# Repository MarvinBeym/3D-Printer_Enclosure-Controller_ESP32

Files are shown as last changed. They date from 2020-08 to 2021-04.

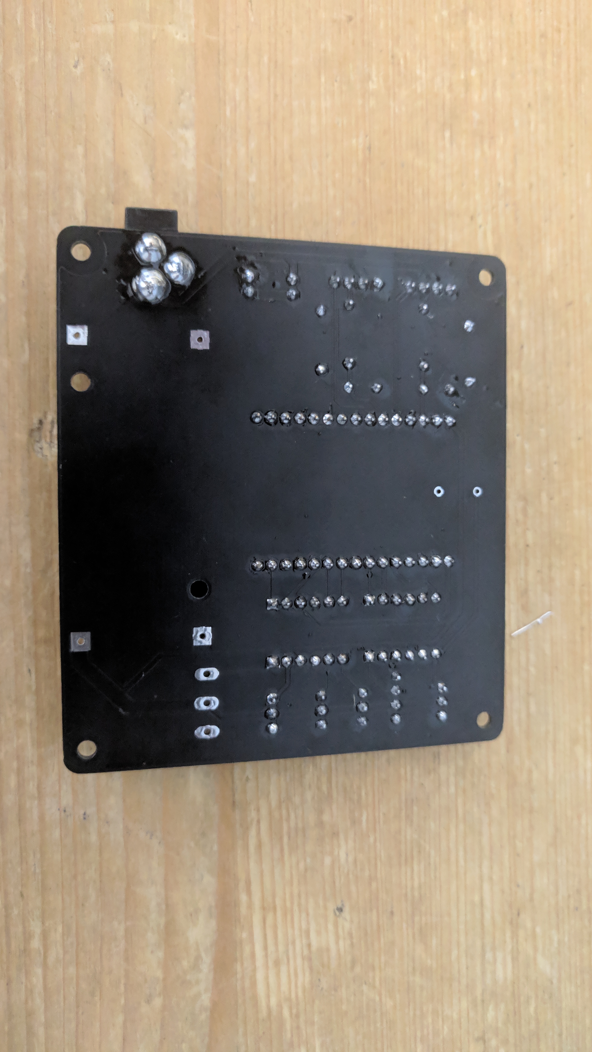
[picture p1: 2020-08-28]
Images/PCB_Fully-Assembled_Back.jpg

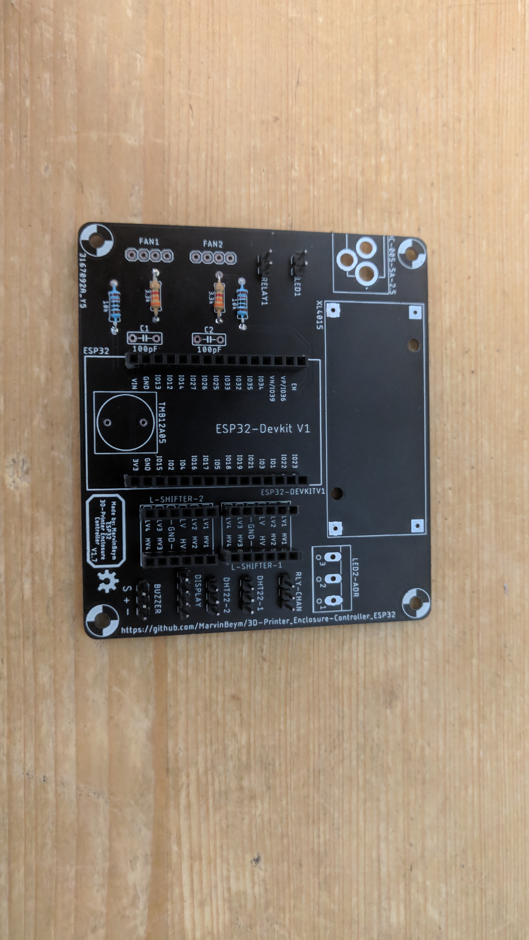
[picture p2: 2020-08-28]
Images/PCB_Assembling.jpg

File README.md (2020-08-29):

# 3D Printer Enclosure Controller ESP32


***
This is an enclosure controller for 3d printers that runs on the dual core ESP32.

- It uses a Nextion NX4832T035 3.5inch 480px320p color touch TFT display.
- It also includes a simple Webinterface made with ESPUI for quick access without having to go to the display.

- ***For detailed information and images please see the [Wiki](https://github.com/MarvinBeym/3D-Printer_Enclosure-Controller_ESP32/wiki "Wiki").***
- ***STL files for 3D-Printing can be found on [Thingiverse](https://www.thingiverse.com/thing:4582196 "Thingiverse")***
***
You can currently choose between 2 versions.
1. The older cnc version
This is a bit older (the first one I made). Features haven't changed yet.
This is the version you want If you want to mill the pcb with a cnc mill because it is single side and has wider traces to make it easier for your mill.
2. The newest, pretiest pcb version
This is supposed to be made by a pcb factory like jlcpcb
It has text on it for all the components.
It also looks way better (I recommend ordering in black :D)

If you choose 2. -> I ordered mine from JLCPCB. The Gerber files are inside the Eagle folder (Gerber(vx.x.x).7z)
These were exported with the premade jlcpcb double sided cam processor. So you can just upload them to jlcpcb and order them.

***This project consists of 4 parts.***
1. The ESP32 software.
2. The Nextion display software (text, icons, images, ...).
3. The PCB.
4. The 3D Printed case to house everything.

***Features of this controller are:***
- 2x temperature and humidity sensors (DHT22).
- 2x 4-pin pwm fans.
- 1x Buzzer for alarms, warnings and such (currently not implemented as of v1.3.1).
- 1x 12v led strip connection controlled by a relay. This is usefull if you want to have a single color (like white).
- 1x 5V WS2812B single addressable led strip

***Software features:***
- ESPUI webinterface
- WifiManager creates a hotspot you can connect to that will make it possible to set the wifi network to connect to on boot.
- All values that can be changed can also be stored to flash. These values will be retrieved at boot and only saved using button pressed to prevent flash wear.
- Displaying of fan speed and percent.
- The possibility to change the speed of fans from 0% - 100%
- Displaying of sensor humidity and temperature
- Switching of 12v led strip.
- Graph for temperatures (only nextion display currently)
- Multiple modes choosable for WS2812B
  - (rainbow, fate, pulse, temperature (led strip is split in half showing temperature in color), running)
- Multiple colors choosable for WS2812B
- LCD Brighness
- LCD Sleep
- Temperature Warning and Danger 
  - (Currently do the same)
  - At some point Danger warning is supposed to do everything to make your notice something going wrong.
  - Like buzzer alarm, led blinking, display blinking and such. This is supposed to be used when something is seriously wrong > xyzTemperature.

***Notices:***
- The board uses a XL4015 buck converter which is rated for ~5A of power. 
- Make sure to choose an led strip that won't overload the converter. As this could lead to overheating.
- Also make sure to leave a bit of room for all other components like fans, 12v led strip, sensors and display.

- It is expecially important to make sure the Nextion display gets enough power.
- If your display starts showing weird graphics. DISCONNECT power immediately.
- Don't run the pcb from 5V pc usb port.
- Low current can destroy the display (although it never happened to me).

- Fan rpm could be off a bit as tacho reading is influenced by noise.
- The tacho ports both have an rc filter and most fans will work without a problem and will display the correct value.
- I have one fan (NF-F12 industrialPPC-3000) that will always display > 4500rpm. 
  - (should only have 3000rpm). 
  - I'm not sure if that is something caused by the fan itself.

***Credits:***
- Icons shown on the Nextion display are from https://icons8.com/

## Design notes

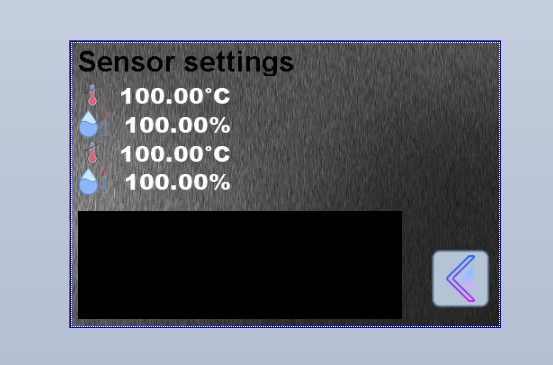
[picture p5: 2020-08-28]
Images/Software_Sensor-Page.jpg

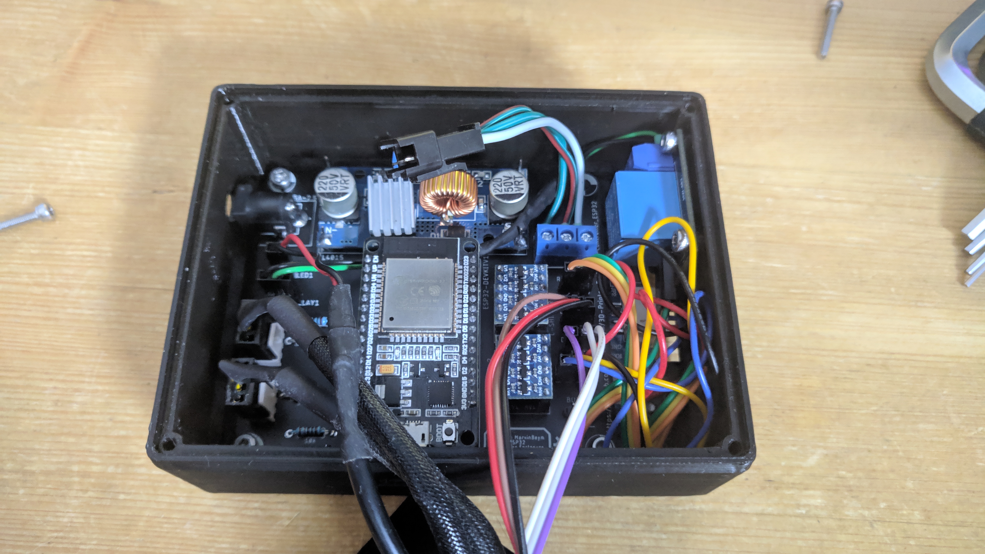
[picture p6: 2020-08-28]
Images/Enclosure_Inside_PCB.jpg

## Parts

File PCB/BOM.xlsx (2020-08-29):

This file includes all components needed to assemble the pcb
Based on pcb version: 1.7.1
PCB itself
Position | Amount | Name | Value | Where to get (mostly banggood -> depending on your location you should look at mouser, digikey or amazon)
R1, R3 |  | Resistor 0207/10 or probably any other | 3.3k Ohm | https://www.banggood.com/Wholesale-Geekcreit-600pcs-30-Kinds-Value-1-pencent-1-or-4W-Metal-Film-Resistor-Assorted-Kit-20pcs-Each-Value-p-53320.html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
R2, R4 |  | Resistor 0207/10 or probably any other | 10k Ohm
C1, C2 |  | Condensator C050-025X075 or probably any other | 100pF | https://www.banggood.com/1000Pcs-50-Value-50V-Ceramic-Capacitor-Assorted-Assortment-Kit-p-1032362.html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
XL4015 | 1 | XL4015 buck converter (not the single chip) |  | https://www.banggood.com/XL4015-5A-DC-DC-Step-Down-Adjustable-Power-Supply-Module-Buck-Converter-p-945599.html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
DC-005-5A-2.5 | 1 | DC-005-5A-2.5 dc jack | 5A | https://lcsc.com/product-detail/AC-DC-Power-Plugs-Receptacles_XKB-Connectivity-DC-005-5A-2-5_C381115.html
LED2-ADR | 1 | 3-Pin W237-103 = Screw terminal |  | https://www.banggood.com/10pcs-5mm-KF-301-3-Pin-PCB-Mount-Block-Screw-Terminal-NF-Connector-p-1136709.html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
IN+, IN-, OUT+, OUT- | 4 | 1-Pin Male Header |  | https://www.banggood.com/10Pcs-40-Pin-2_54mm-Male-Female-SIL-Socket-Row-Strip-PCB-Connector-p-953436.html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
LED1, RELAY1 | 2 | 2-Pin Male Header
RLY-CHAN, DHT22-1, DHT22-2, BUZZER | 4 | 3-Pin Male Header
DISPLAY, FAN1, FAN2 | 3 | 4-Pin Male Header
L-SHIFTER-1, L-SHIFTER-2 | 4 | 6-Pin Female Header
ESP32 | 2 | 15-Pin Female Header
Other components (You can choose less/none for some)
can be less | 2 | DHT22 Temperature and Humidity Sensor (with Pullup on sensor) (you can solder your own pullup | NEEDS PULLUP | https://www.banggood.com/3Pcs-AM2302-DHT22-Temperature-And-Humidity-Sensor-Module-p-1006452.html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
can be none | 1 | KY-019 (or any other) Relay (for 12V led |  | https://www.banggood.com/3Pcs-5V-Relay-5-12V-TTL-Signal-1-Channel-Module-High-Level-Expansion-Board-p-1178211.html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
can be less/none | 2 | 4-Pin PWM fans |  | Choose your own
needed | 1 | ESP32 (30pin) |  | https://www.banggood.com/Geekcreit-ESP32-WiFi+bluetooth-Development-Board-Ultra-Low-Power-Consumption-Dual-Cores-Pins-Unsoldered-p-1214159.html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
can be none | 1 | Buzzer (no use currently) either connected to BUZZER or below esp32 |  | Choose your own
needed | 1 | 12 Power supply >5A | Recommend > 5A | Choose your own
can be none | 1 | WS2812B | DONT BUY RGBW | Choose your own based on liking
can be none | 1 | 12v Led strip |  | Choose your own based on liking
needed | 2 | Bi-Direktional 4 Channel Level Shifter |  | https://www.banggood.com/Logic-Level-Converter-Bi-Directional-IIC-4-Way-Level-Conversion-Module-p-938774.html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

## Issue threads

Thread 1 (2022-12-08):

Nextion Display setup for NX4832F035 model

Pilgrim182551, 2022-12-08:
Mea Culpa ... I bought  NX4832F035 model instead of NX4832T035. Is there any chance to compile tft file for my "F" model? After applaying sd card with NextionDesignerFile.v1.3.1.tft display returns "Model does not match Device Model: NX4832F035_011R" ... Thx

MarvinBeym, 2022-12-29:
(Again note that this project is basically abandoned as Klipper makes everything easier & better)

1. Download the project => https://github.com/MarvinBeym/3D-Printer_Enclosure-Controller_ESP32 => "Code" => "Download Zip"
3. Extract somewhere (For this issue you only need the `Display` folder)
4. Download the NextionEditor: https://nextion.tech/nextion-editor/
5. Inside NextionEditor. Open the `NextionDesignerFile.HMI` file from the `Display` folder.
6. Once opened. At the top right you will find a `Device` button.
7. Switch to the `Device` menu
8. Change to the display you have.
9. You may have to change other things if the display is for example larger (most likely not relevant in this case)
10. Click on the `File` button at the top left of the main editor window.
11. Click on `TFT output`.
12. This should then give you the file to flash using the sd card

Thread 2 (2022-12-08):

Esp32 controller setup

Pilgrim182551, 2022-12-08:
VSC/Platformio compiler/linker return a number errors related to inconsistent libraries(littleFS) and process end up with red alert collect2.exe: error: ld returned 1 exit status
*** [.pio\build\esp32doit-devkit-v1\firmware.elf] Error 1

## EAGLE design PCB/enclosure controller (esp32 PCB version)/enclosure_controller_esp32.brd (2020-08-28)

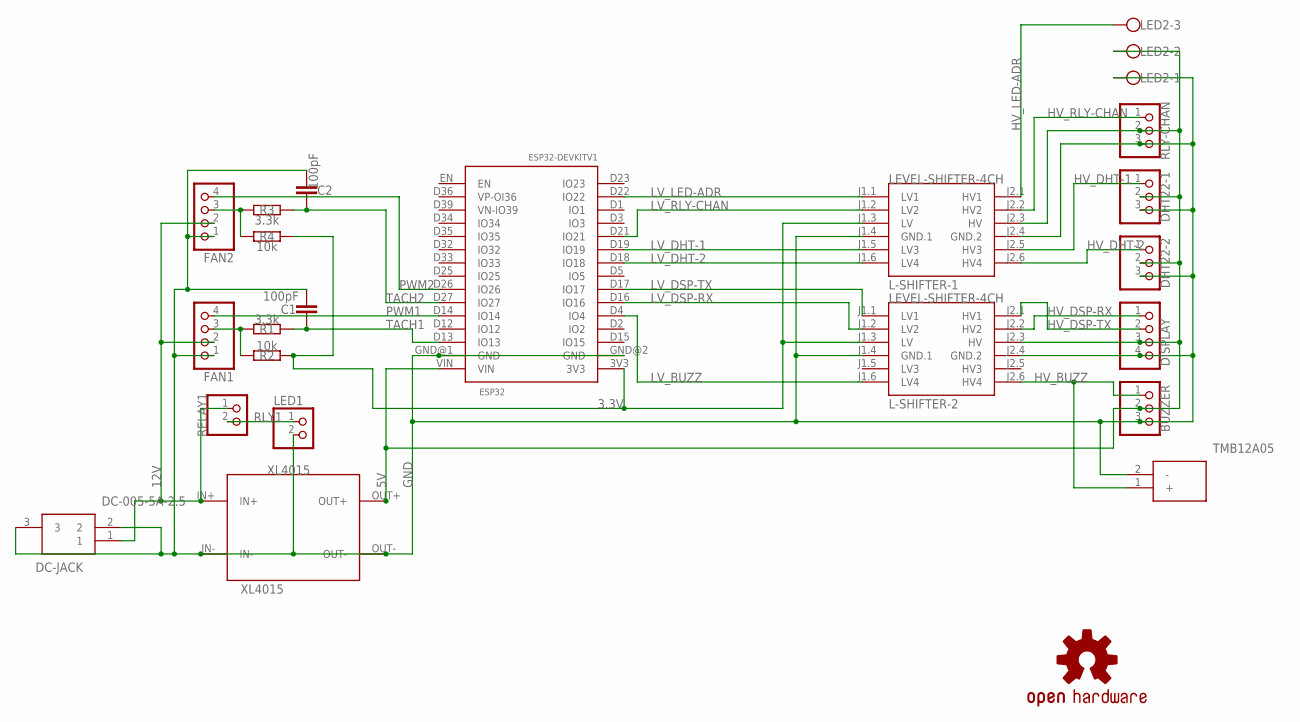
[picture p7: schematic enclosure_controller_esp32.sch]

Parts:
BUZZER: PINHD-1X3/OCT; 1X03/OCT
C1, C2: 100pF; C050-025X075
DC-JACK: DC-005-5A-2.5; DC0055A25
DHT22-1, DHT22-2: PINHD-1X3/OCT; 1X03/OCT
DISPLAY: PINHD-1X4/OCT; 1X04/OCT
ESP32: ESP32DEVKITV1; ESP32-DEVKITV1
FAN1, FAN2: PINHD-1X4/OCT; 1X04/OCT
L-SHIFTER-1, L-SHIFTER-2: LEVEL-SHIFTER-4CH
LED1: PINHD-1X2/OCT; 1X02/OCT
LED2: LED2-ADR; W237-103
LOGO1: OSHW-LOGOM; OSHW-LOGO-M
LS1: TMB12A05
R1, R3: 3.3k; 0207/10
R2, R4: 10k; 0207/10
RELAY1: PINHD-1X2/OCT; 1X02/OCT
RLY-CHAN: PINHD-1X3/OCT; 1X03/OCT
XL4015: XL4015

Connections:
3.3V: ESP32.3V3, L-SHIFTER-1.J1.3 (LV), L-SHIFTER-2.J1.3 (LV), R2.1, R4.1
5V: BUZZER.2, DHT22-1.2, DHT22-2.2, DISPLAY.3, ESP32.VIN, L-SHIFTER-1.J2.3 (HV), L-SHIFTER-2.J2.3 (HV), LED2.2, RLY-CHAN.2, XL4015.OUT+
12V: DC-JACK.1, FAN1.2, FAN2.2, RELAY1.1, XL4015.IN+
GND: BUZZER.3, C1.2, C2.1, DC-JACK.2, DC-JACK.3, DHT22-1.3, DHT22-2.3, DISPLAY.4, ESP32.GND@1 (GND), ESP32.GND@2 (GND), FAN1.1, FAN2.1, L-SHIFTER-1.J1.4 (GND.1), L-SHIFTER-1.J2.4 (GND.2), L-SHIFTER-2.J1.4 (GND.1), L-SHIFTER-2.J2.4 (GND.2), LED1.2, LED2.1, LS1.2 (-), RLY-CHAN.3, XL4015.IN-, XL4015.OUT-
HV_BUZZ: BUZZER.1, L-SHIFTER-2.J2.6 (HV4), LS1.1 (+)
HV_DHT-1: DHT22-1.1, L-SHIFTER-1.J2.5 (HV3)
HV_DHT-2: DHT22-2.1, L-SHIFTER-1.J2.6 (HV4)
HV_DSP-RX: DISPLAY.1, L-SHIFTER-2.J2.2 (HV2)
HV_DSP-TX: DISPLAY.2, L-SHIFTER-2.J2.1 (HV1)
HV_LED-ADR: L-SHIFTER-1.J2.1 (HV1), LED2.3
HV_RLY-CHAN: L-SHIFTER-1.J2.2 (HV2), RLY-CHAN.1
LV_BUZZ: ESP32.D4 (IO4), L-SHIFTER-2.J1.6 (LV4)
LV_DHT-1: ESP32.D19 (IO19), L-SHIFTER-1.J1.5 (LV3)
LV_DHT-2: ESP32.D18 (IO18), L-SHIFTER-1.J1.6 (LV4)
LV_DSP-RX: ESP32.D16 (IO16), L-SHIFTER-2.J1.2 (LV2)
LV_DSP-TX: ESP32.D17 (IO17), L-SHIFTER-2.J1.1 (LV1)
LV_LED-ADR: ESP32.D22 (IO22), L-SHIFTER-1.J1.1 (LV1)
LV_RLY-CHAN: ESP32.D21 (IO21), L-SHIFTER-1.J1.2 (LV2)
PWM1: ESP32.D14 (IO14), FAN1.4
PWM2: ESP32.D26 (IO26), FAN2.4
RLY1: LED1.1, RELAY1.2
TACH1: C1.1, ESP32.D13 (IO13), FAN1.3, R1.1, R1.2, R2.2
TACH2: C2.2, ESP32.D27 (IO27), FAN2.3, R3.1, R3.2, R4.2

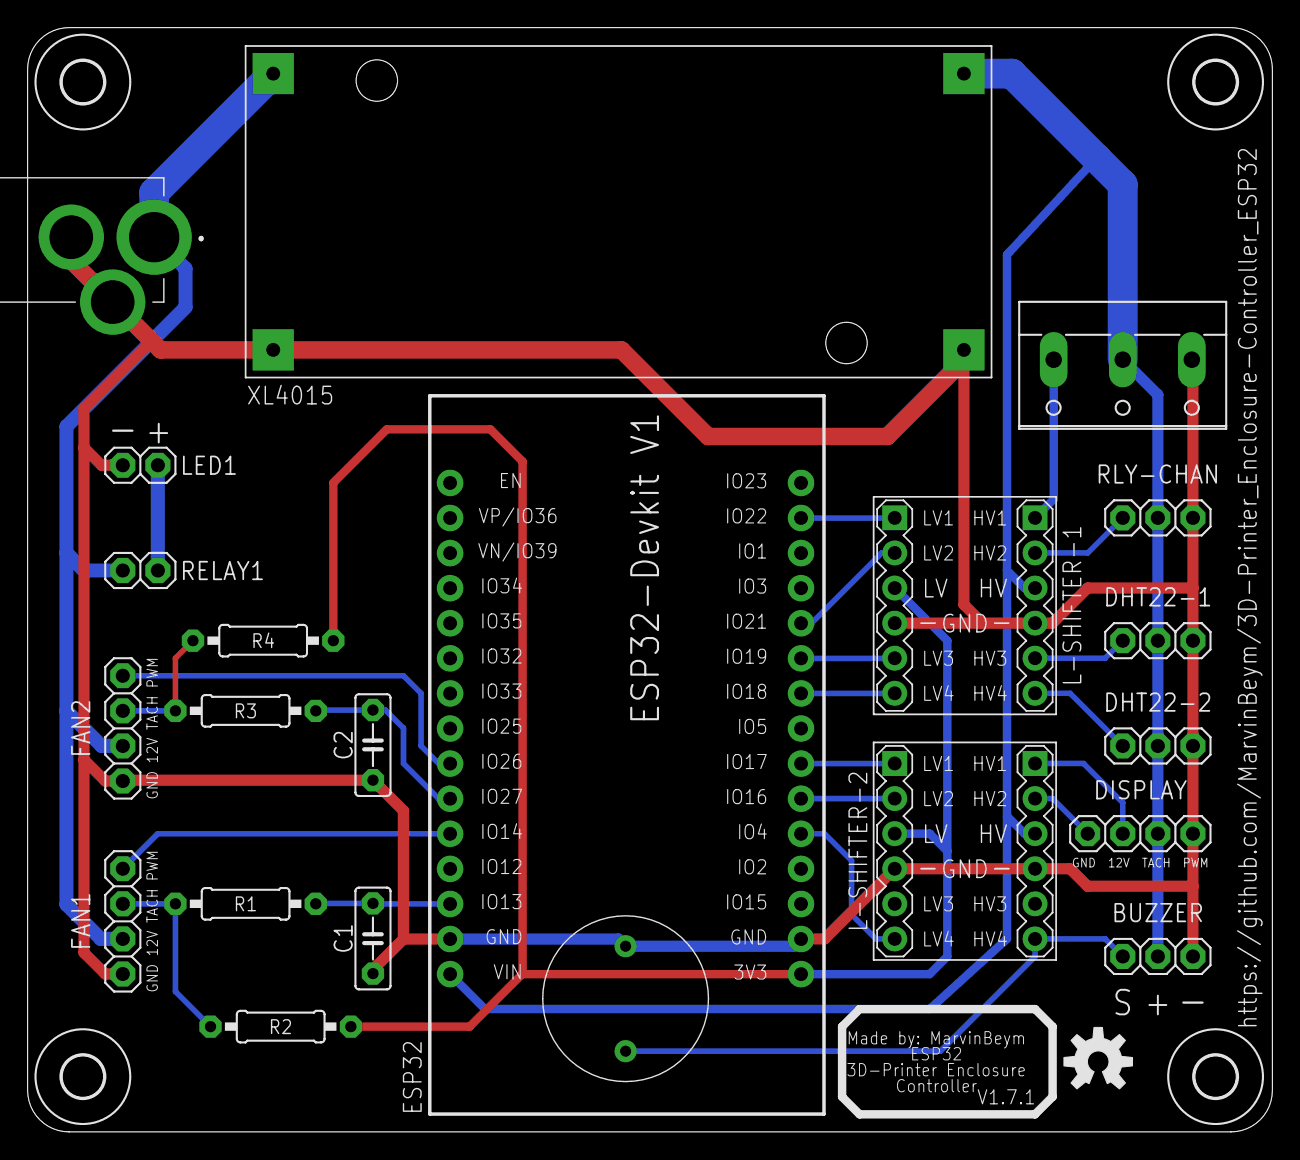
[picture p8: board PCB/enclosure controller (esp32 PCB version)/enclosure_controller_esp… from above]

Board: 2 copper layers, 90.1 x 79.9 mm, 27 parts (0 on the bottom side), 23 nets.

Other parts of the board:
U$1, U$2, U$3, U$4: 3,0

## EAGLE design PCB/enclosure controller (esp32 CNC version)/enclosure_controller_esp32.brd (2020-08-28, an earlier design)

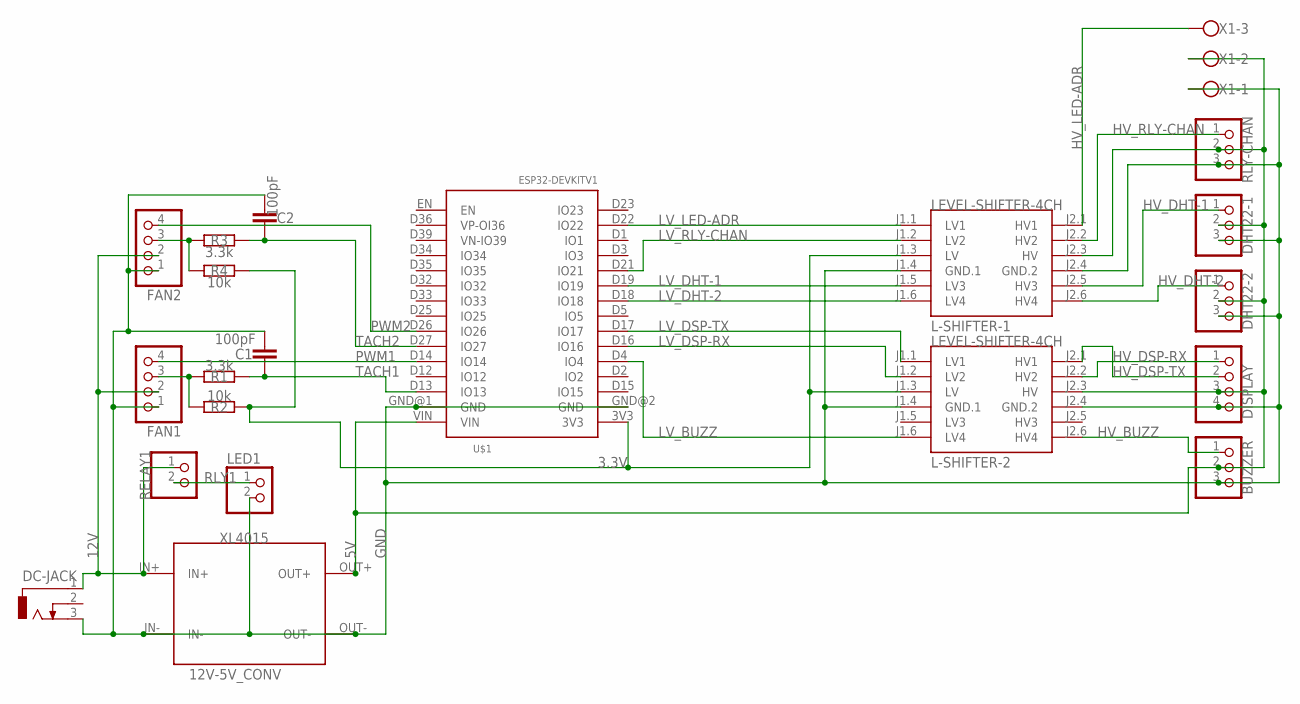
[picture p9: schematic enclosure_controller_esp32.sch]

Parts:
12V-5V_CONV: XL4015
BUZZER: PINHD-1X3; 1X03
C1, C2: 100pF; C050-025X075
DC-JACK: DCJ0303
DHT22-1, DHT22-2: PINHD-1X3; 1X03
DISPLAY: PINHD-1X4; 1X04
FAN1, FAN2: PINHD-1X4; 1X04
L-SHIFTER-1, L-SHIFTER-2: LEVEL-SHIFTER-4CH
LED1: PINHD-1X2; 1X02
R1, R3: 3.3k; 0207/10
R2, R4: 10k; 0207/10
RELAY1: PINHD-1X2; 1X02
RLY-CHAN: PINHD-1X3; 1X03
U$1: ESP32DEVKITV1; ESP32-DEVKITV1
X1: LED2-ADR; W237-103

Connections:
3.3V: L-SHIFTER-1.J1.3 (LV), L-SHIFTER-2.J1.3 (LV), R2.1, R4.1, U$1.3V3
5V: 12V-5V_CONV.OUT+, BUZZER.2, DHT22-1.2, DHT22-2.2, DISPLAY.3, L-SHIFTER-1.J2.3 (HV), L-SHIFTER-2.J2.3 (HV), RLY-CHAN.2, U$1.VIN, X1.2
12V: 12V-5V_CONV.IN+, DC-JACK.1, FAN1.2, FAN2.2, RELAY1.1
GND: 12V-5V_CONV.IN-, 12V-5V_CONV.OUT-, BUZZER.3, C1.2, C2.1, DC-JACK.3, DHT22-1.3, DHT22-2.3, DISPLAY.4, FAN1.1, FAN2.1, L-SHIFTER-1.J1.4 (GND.1), L-SHIFTER-1.J2.4 (GND.2), L-SHIFTER-2.J1.4 (GND.1), L-SHIFTER-2.J2.4 (GND.2), LED1.2, RLY-CHAN.3, U$1.GND@1 (GND), U$1.GND@2 (GND), X1.1
HV_BUZZ: BUZZER.1, L-SHIFTER-2.J2.6 (HV4)
HV_DHT-1: DHT22-1.1, L-SHIFTER-1.J2.5 (HV3)
HV_DHT-2: DHT22-2.1, L-SHIFTER-1.J2.6 (HV4)
HV_DSP-RX: DISPLAY.1, L-SHIFTER-2.J2.2 (HV2)
HV_DSP-TX: DISPLAY.2, L-SHIFTER-2.J2.1 (HV1)
HV_LED-ADR: L-SHIFTER-1.J2.1 (HV1), X1.3
HV_RLY-CHAN: L-SHIFTER-1.J2.2 (HV2), RLY-CHAN.1
LV_BUZZ: L-SHIFTER-2.J1.6 (LV4), U$1.D4 (IO4)
LV_DHT-1: L-SHIFTER-1.J1.5 (LV3), U$1.D19 (IO19)
LV_DHT-2: L-SHIFTER-1.J1.6 (LV4), U$1.D18 (IO18)
LV_DSP-RX: L-SHIFTER-2.J1.2 (LV2), U$1.D16 (IO16)
LV_DSP-TX: L-SHIFTER-2.J1.1 (LV1), U$1.D17 (IO17)
LV_LED-ADR: L-SHIFTER-1.J1.1 (LV1), U$1.D22 (IO22)
LV_RLY-CHAN: L-SHIFTER-1.J1.2 (LV2), U$1.D21 (IO21)
PWM1: FAN1.4, U$1.D14 (IO14)
PWM2: FAN2.4, U$1.D26 (IO26)
RLY1: LED1.1, RELAY1.2
TACH1: C1.1, FAN1.3, R1.1, R1.2, R2.2, U$1.D13 (IO13)
TACH2: C2.2, FAN2.3, R3.1, R3.2, R4.2, U$1.D27 (IO27)

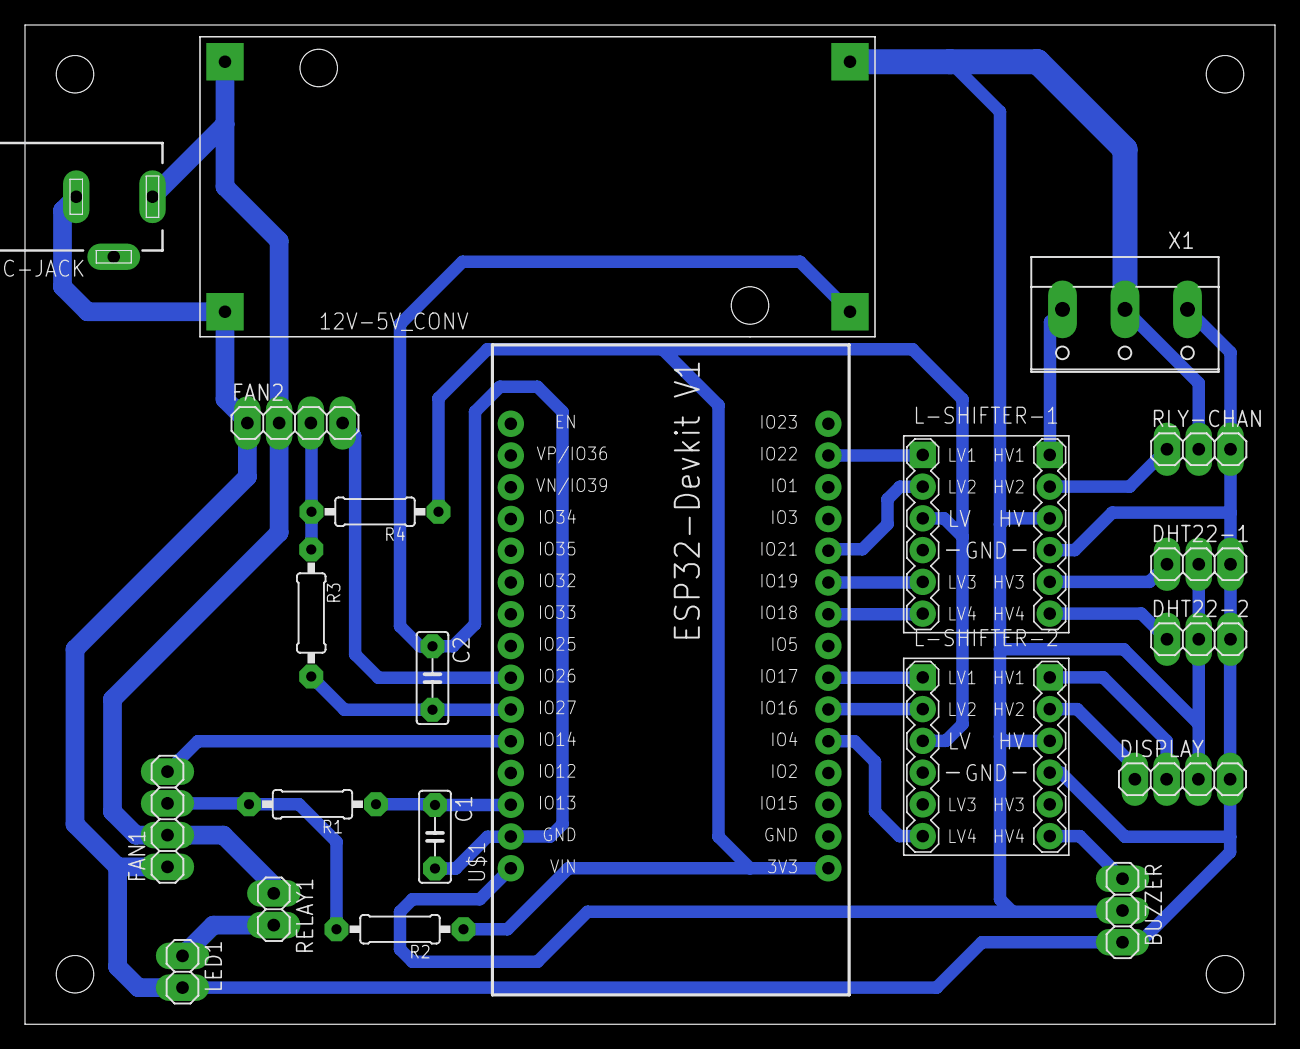
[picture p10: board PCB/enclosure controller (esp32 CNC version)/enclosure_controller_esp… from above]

Board: 2 copper layers, 100.0 x 79.9 mm, 21 parts (0 on the bottom side), 23 nets.

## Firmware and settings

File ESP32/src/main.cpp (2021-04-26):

/**
 * 3D-Printer Enclosure Controller firmware for the ESP32
 * Copyright (C) 2021  Marvin Beym
 *
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
 * You should have received a copy of the GNU General Public License
 * along with this program.  If not, see <https://www.gnu.org/licenses/>.
 **/

#define FASTLED_INTERNAL

#include <Arduino.h>
#include <ESPAsyncWebServer.h>
#include "task-events.h"
#include "helper.h"
#include "controller-pin-definition.h"
#include "controller-configuration.h"

#include "ESP8266React.h"
#include "libs/NextionDisplay.h"
#include "libs/Sensor.h"
#include "libs/Relay.h"
#include "libs/FasterLed.h"
#include "libs/Fan.h"
#include "libs/Config.h"
#include "libs/Buzzer.h"
#include "effects/EffectLoader.h"

EventGroupHandle_t eg;

AsyncWebSocket ws("/ws");
AsyncWebServer server(80);
ESP8266React esp8266React(&server);

Sensor *sensor1;
Sensor *sensor2;
Relay *led1;
FasterLed *led2;
Fan *fan1;
Fan *fan2;
EffectLoader *effectLoader;
Buzzer *buzzer;
Config *config;
bool booted = false;

NextionDisplay *nextion;

void onWsEvent(AsyncWebSocket *webSocket, AsyncWebSocketClient *client, AwsEventType type, void *arg, uint8_t *data,
			   size_t len);

enum WebSocketComponent
{
	Led1,
	Led2,
	Fan1,
	Fan2,
	Configuration,
	Sensor1,
	Sensor2,
	Invalid,
};

enum WebSocketCommand
{
	setState,
	setEffect,
	setPercent,
	setEffectConfig,
	setDisplayBrightness,
	setDisplaySleep,
	setTempDangerEnabled,
	setTempDangerThreshold,
	invalid,
};

WebSocketComponent resolveWebSocketComponent(String component)
{
	if (component == "led1") return Led1;
	if (component == "led2") return Led2;
	if (component == "fan1") return Fan1;
	if (component == "fan2") return Fan2;
	if (component == "configuration") return Configuration;
	if (component == "sensor1") return Sensor1;
	if (component == "sensor2") return Sensor2;
	return Invalid;
}

WebSocketCommand resolveWebSocketCommand(String command)
{
	if (command == "setState") return setState;
	if (command == "setEffect") return setEffect;
	if (command == "setPercent") return setPercent;
	if (command == "setEffectConfig") return setEffectConfig;
	if (command == "setDisplayBrightness") return setDisplayBrightness;
	if (command == "setDisplaySleep") return setDisplaySleep;
	if (command == "setTempDangerEnabled") return setTempDangerEnabled;
	if (command == "setTempDangerThreshold") return setTempDangerThreshold;
	return invalid;
}

void IRAM_ATTR fan1TachoInterrupt()
{
	BaseType_t xHigherPriorityTaskWoken, xResult;
	xHigherPriorityTaskWoken = pdFALSE;

	if (fan1->halfRevolutions >= fanSenseInterval) {
		xResult = xEventGroupSetBitsFromISR(eg, TASK_EVENT_FAN1_CalcRpm, &xHigherPriorityTaskWoken);
		if (xResult != pdFAIL) {
			portYIELD_FROM_ISR();
		}
	} else {
		fan1->halfRevolutions++;
	}
}

void IRAM_ATTR fan2TachoInterrupt()
{
	BaseType_t xHigherPriorityTaskWoken, xResult;
	xHigherPriorityTaskWoken = pdFALSE;

	if (fan2->halfRevolutions >= fanSenseInterval) {
		xResult = xEventGroupSetBitsFromISR(eg, TASK_EVENT_FAN2_CalcRpm, &xHigherPriorityTaskWoken);
		if (xResult != pdFAIL) {
			portYIELD_FROM_ISR();
		}
	} else {
		fan2->halfRevolutions++;
	}
}

void sensor1TemperatureUpdated(void *params)
{
	for (;;) {
		xEventGroupWaitBits(eg, TASK_EVENT_SENSOR1_TemperatureUpdated, pdTRUE, pdTRUE, portMAX_DELAY);
		float temperature = *((float *) params);


		String value = Helper::Helper::valueToTempString(temperature);
		nextion->setCompText("main_page.tf_temp_sens1", value);
		nextion->setCompText("sensor_page.tf_temp_sens1", value);
		nextion->addGraphValue(
				1, 0,
				Helper::newMap((int) temperature, displayGraphMinTemp, 255, 0, displayGraphHeight));
		DynamicJsonDocument json(64);
		sensor1->addToJson(&json, true, false, false);
		String response;
		serializeJson(json, response);

		ws.textAll(response);
		delay(10);
	}
}

void sensor1HumidityUpdated(void *params)
{
	for (;;) {
		xEventGroupWaitBits(eg, TASK_EVENT_SENSOR1_HumidityUpdated, pdTRUE, pdTRUE, portMAX_DELAY);
		float humidity = *((float *) params);

		String value = Helper::valueToPercentString(humidity);
		nextion->setCompText("main_page.tf_hum_sens1", value);
		nextion->setCompText("sensor_page.tf_hum_sens1", value);

		DynamicJsonDocument json(64);
		sensor1->addToJson(&json, false, true, false);
		String response;
		serializeJson(json, response);

		ws.textAll(response);
		delay(10);
	}
}

void sensor1TempWarnUpdated(void *params) {
	for (;;) {
		xEventGroupWaitBits(eg, TASK_EVENT_SENSOR1_TempWarnUpdated, pdTRUE, pdTRUE, portMAX_DELAY);

		DynamicJsonDocument json(192);
		sensor1->addToJson(&json, false, false, true);

		String response;
		serializeJson(json, response);

		ws.textAll(response);
		delay(10);
	}
}

void sensor2TemperatureUpdated(void *params)
{
	for (;;) {
		xEventGroupWaitBits(eg, TASK_EVENT_SENSOR2_TemperatureUpdated, pdTRUE, pdTRUE, portMAX_DELAY);
		float temperature = *((float *) params);

		String value = Helper::valueToTempString(temperature);
		nextion
				->setCompText("main_page.tf_temp_sens2", value)
				->setCompText("sensor_page.tf_temp_sens2", value)
				->addGraphValue(
						1, 1,
						Helper::newMap((int) temperature, displayGraphMinTemp, 255, 0, displayGraphHeight));
		DynamicJsonDocument json(64);
		sensor2->addToJson(&json, true, false, false);
		String response;
		serializeJson(json, response);

		ws.textAll(response);
		delay(10);
	}
}

void sensor2HumidityUpdated(void *params)
{
	for (;;) {
		xEventGroupWaitBits(eg, TASK_EVENT_SENSOR2_HumidityUpdated, pdTRUE, pdTRUE, portMAX_DELAY);
		float humidity = *((float *) params);

		String value = Helper::valueToPercentString(humidity);
		nextion
				->setCompText("main_page.tf_hum_sens2", value)
				->setCompText("sensor_page.tf_hum_sens2", value);

		DynamicJsonDocument json(64);
		sensor2->addToJson(&json, false, true, false);
		String response;
		serializeJson(json, response);

		ws.textAll(response);
		delay(10);
	}
}

void sensor2TempWarnUpdated(void *params) {
	for (;;) {
		xEventGroupWaitBits(eg, TASK_EVENT_SENSOR2_TempWarnUpdated, pdTRUE, pdTRUE, portMAX_DELAY);

		DynamicJsonDocument json(192);
		sensor2->addToJson(&json, false, false, true);

		String response;
		serializeJson(json, response);

		ws.textAll(response);
		delay(10);
	}
}

void fan1RpmUpdated(void *params)
{
	for (;;) {
		xEventGroupWaitBits(eg, TASK_EVENT_FAN1_RpmUpdated, pdTRUE, pdTRUE, portMAX_DELAY);
		int rpm = *((int *) params);

		String value = Helper::valueToRpmString(rpm);

		nextion
				->setCompText("main_page.tf_speed_fan1", value)
				->setCompText("fans_page.tf_speed_fan1", value);

		DynamicJsonDocument json(64);
		fan1->addToJson(&json, true, false, false);
		String response;
		serializeJson(json, response);

		ws.textAll(response);
		delay(10);
	}
}

void fan1PwmUpdated(void *params)
{
	for (;;) {
		xEventGroupWaitBits(eg, TASK_EVENT_FAN1_PwmUpdated, pdTRUE, pdTRUE, portMAX_DELAY);
		int percent = fan1->getPercent();

		String value = Helper::valueToPercentString(percent);
		nextion
				->setCompText("main_page.tf_pwm_fan1", value)
				->setCompText("fans_page.tf_pwm_fan1", value)
				->setCompValue("fans_page.sli_speed_fan1", percent);

		DynamicJsonDocument json(64);
		fan1->addToJson(&json, false, true, true);
		String response;
		serializeJson(json, response);

		ws.textAll(response);
		delay(10);
	}
}

void fan2RpmUpdated(void *params)
{
	for (;;) {
		xEventGroupWaitBits(eg, TASK_EVENT_FAN2_RpmUpdated, pdTRUE, pdTRUE, portMAX_DELAY);
		int rpm = *((int *) params);

		String value = Helper::valueToRpmString(rpm);
		nextion
				->setCompText("main_page.tf_speed_fan2", value)
				->setCompText("fans_page.tf_speed_fan2", value);

		DynamicJsonDocument json(64);
		fan2->addToJson(&json, true, false, false);
		String response;
		serializeJson(json, response);

		ws.textAll(response);
		delay(10);
	}
}

void fan2PwmUpdated(void *params)
{
	for (;;) {
		xEventGroupWaitBits(eg, TASK_EVENT_FAN2_PwmUpdated, pdTRUE, pdTRUE, portMAX_DELAY);
		//int dutyCycle = fan2->getDutyCycle();
		int percent = fan2->getPercent();

		String value = Helper::valueToPercentString(percent);
		nextion
				->setCompText("main_page.tf_pwm_fan2", value)
				->setCompText("fans_page.tf_pwm_fan2", value)
				->setCompValue("fans_page.sli_speed_fan2", percent);

		DynamicJsonDocument json(64);
		fan2->addToJson(&json, false, true, true);
		String response;
		serializeJson(json, response);

		ws.textAll(response);
		delay(10);
	}
}

void led1StateUpdated(void *params)
{
	for (;;) {
		xEventGroupWaitBits(eg, TASK_EVENT_LED1_StateUpdated, pdTRUE, pdTRUE, portMAX_DELAY);
		bool state = *((bool *) params);

		nextion->setCompValue("led_page.btn_led1", state ? 1 : 0);

		DynamicJsonDocument json(128);
		led1->addToJson(&json);
		String response;
		serializeJson(json, response);

		ws.textAll(response);
		delay(10);
	}
}

void nextionCompClickedCallback(void *params)
{
	for (;;) {
		xEventGroupWaitBits(eg, TASK_EVENT_NEXTION_CompClicked, pdTRUE, pdTRUE, portMAX_DELAY);
		const int pageId = nextion->compClicked_pageId;
		const int compId = nextion->compClicked_compId;

		nextion->compClicked_pageId = -1;
		nextion->compClicked_compId = -1;

		switch (pageId) {
			case MAIN_PAGE:
				switch (compId) {
					case 1:
						nextion->setPage(FANS_PAGE);
						break;
					case 2:
						nextion->setPage(SENSOR_PAGE);
						break;
					case 3:
						nextion->setPage(LED_PAGE);
						break;
					case 4:
						nextion->setPage(CONF_PAGE);
				}
				break;
			case FANS_PAGE:
				switch (compId) {
					case 3:
						delay(20);
						fan2->setPercent(nextion->getCompValue("fans_page.sli_speed_fan2"));
						delay(20);

						break;
					case 4:
						delay(20);
						fan1->setPercent(nextion->getCompValue("fans_page.sli_speed_fan1"));
						delay(20);
						break;
					case 6:
						nextion->setPage(MAIN_PAGE);
						break;
				}
				break;
			case SENSOR_PAGE:
				switch (compId) {
					case 2:
						nextion->setPage(MAIN_PAGE);
						break;
				}
				break;
			case LED_PAGE:
				switch (compId) {
					case 1:
						led1->setState(nextion->getCompValue("led_page.btn_led1"));
						break;

					case 11:
						effectLoader->changeEffect(effectLoader->getCurrentEffect() + 1);
						break;
					case 12:
						effectLoader->changeEffect(effectLoader->getCurrentEffect() - 1);
						break;
					case 14:
						nextion->setPage(MAIN_PAGE);
						break;
				}
				break;
			case CONF_PAGE:
				switch (compId) {
					case 1:
						nextion->setPage(MAIN_PAGE);
						break;
					case 2:
						nextion->setPage(ABOUT_PAGE);
						break;
					case 3:
						config->setDisplayBrightness(nextion->getCompValue("conf_page.sli_brightness"));
						break;
					case 4:
						config->setDisplaySleep(nextion->getCompValue("conf_page.btn_sleep"));
				}
				break;
			case ABOUT_PAGE:
				switch (compId) {
					case 6:
						nextion->setPage(CONF_PAGE);
						break;
				}
				break;
		}
	}
}

void effectChangeCallback(void *params)
{
	for (;;) {
		xEventGroupWaitBits(eg, TASK_EVENT_LED2_EffectChanged, pdTRUE, pdTRUE, portMAX_DELAY);
		int newEffectId = *((int *) params);

		nextion->setCompText("led_page.tf_mode", effectLoader->getEffectName(newEffectId, true));

		DynamicJsonDocument json(96);
		effectLoader->addToJson(&json, true, false);
		String response;
		serializeJson(json, response);

		ws.textAll(response);

		delay(10);
	}
}

void configUpdated(void *params)
{
	for (;;) {
		xEventGroupWaitBits(eg, TASK_EVENT_ConfigUpdate, pdTRUE, pdTRUE, portMAX_DELAY);

		String command = "dims=";
		command += config->getDisplayBrightness();
		nextion->sendCommand(command.c_str());

		if(config->getDisplaySleep()) {
			nextion->sendCommand("thsp=10");
		} else {
			nextion->sendCommand("sleep=0");
			nextion->sendCommand("thsp=0");
		}

		//Delay to make sure the screen starts accepting commands to change component values after sleep update
		delay(10);

		nextion->setCompValue("conf_page.sli_brightness", config->getDisplayBrightness());
		nextion->setCompValue("conf_page.btn_sleep", config->getDisplaySleep());

		DynamicJsonDocument json(256);
		config->addToJson(&json);

		String response;
		serializeJson(json, response);

		ws.textAll(response);

		delay(10);
	}
}

void setup()
{
	Serial.begin(serial1BaudRate);
	while (!Serial) {}
	Serial.println("3D-Print-Enclosure-Controller booting v" + esp32Version);
	delay(100);
	eg = xEventGroupCreate();

	//Temp & Humidity sensor setup
	sensor1 = new Sensor(
			"sensor1",
			dht22_1_pin,
			dhtSenseInterval,
			eg,
			TASK_EVENT_SENSOR1_TemperatureUpdated,
			TASK_EVENT_SENSOR1_HumidityUpdated,
			TASK_EVENT_SENSOR1_TempWarnUpdated,
			&sensor1TemperatureUpdated,
			&sensor1HumidityUpdated,
			&sensor1TempWarnUpdated
	);
	sensor2 = new Sensor(
			"sensor2",
			dht22_2_pin,
			dhtSenseInterval,
			eg,
			TASK_EVENT_SENSOR2_TemperatureUpdated,
			TASK_EVENT_SENSOR2_HumidityUpdated,
			TASK_EVENT_SENSOR2_TempWarnUpdated,
			&sensor2TemperatureUpdated,
			&sensor2HumidityUpdated,
			&sensor2TempWarnUpdated
	);

	//Led1 (relay) setup
	led1 = new Relay("led1", led1_relay_pin, eg, TASK_EVENT_LED1_StateUpdated, &led1StateUpdated);

	//Led2 (WS2812B) setup
	led2 = new FasterLed(led2_data_pin, led2NumberOfLeds, led2Brightness, led2CurrentLimit);
	FastLED.addLeds<WS2812B, led2_data_pin, GRB>(led2->leds, led2NumberOfLeds);
	led2->begin();
	effectLoader = new EffectLoader(led2, eg, TASK_EVENT_LED2_EffectChanged, &effectChangeCallback);

	//Configuration
	config = new Config(eg, &configUpdated);

	//Fan
	fan1 = new Fan(
			"fan1",
			0,
			eg,
			TASK_EVENT_FAN1_CalcRpm,
			TASK_EVENT_FAN1_RpmUpdated,
			TASK_EVENT_FAN1_PwmUpdated,
			fan1_tacho_pin,
			fan1_pwm_pin,
			&fan1RpmUpdated,
			&fan1PwmUpdated
	);
	fan2 = new Fan(
			"fan2",
			1,
			eg,
			TASK_EVENT_FAN2_CalcRpm,
			TASK_EVENT_FAN2_RpmUpdated,
			TASK_EVENT_FAN2_PwmUpdated,
			fan2_tacho_pin,
			fan2_pwm_pin,
			&fan2RpmUpdated,
			&fan2PwmUpdated
	);

	//Buzzer
	buzzer = new Buzzer(buzzer_pin, 2);
	//Display
	nextion = new NextionDisplay(displayBootDelay, serial2BaudRate, nextionDisplayRX, nextionDisplayTX, eg,
								 TASK_EVENT_NEXTION_CompClicked, &nextionCompClickedCallback);

	String version = "ESP32: v";
	version.concat(esp32Version);
	nextion->setCompText("about_page.tf_esp32_v", version);

	esp8266React.begin();
	ws.onEvent(onWsEvent);

	server.addHandler(&ws);
	server.begin();

	//Delay and attaching interrupt after everything is
	//required to prevent crashes from happening on boot caused by weird interrupt stuff

	attachInterrupt(digitalPinToInterrupt(fan1_tacho_pin), fan1TachoInterrupt, FALLING);
	attachInterrupt(digitalPinToInterrupt(fan2_tacho_pin), fan2TachoInterrupt, FALLING);

	Serial.println("3D-Print-Enclosure-Controller booted");
	booted = true;
}

DynamicJsonDocument handleWebSocketCommunication(DynamicJsonDocument json)
{
	String _component = json["component"];
	String _command = json["command"];
	String value = json["value"];

	DynamicJsonDocument responseDoc(1024);
	WebSocketComponent component = resolveWebSocketComponent(_component);
	WebSocketCommand command = resolveWebSocketCommand(_command);

	if (command == WebSocketCommand::invalid) {
		responseDoc["message"] = "Invalid command";
		responseDoc["status"] = "failure";
		responseDoc["command"] = _command;
		return responseDoc;
	}

	switch (component) {
		case Led1:
			if (command == setState) {
				int newState = value.toInt();
				led1->setState(newState);
			}
			break;
		case Led2:
			if (command == setEffect) {
				int newEffect = value.toInt();
				effectLoader->changeEffect(newEffect);
			}
			if (command == setEffectConfig) {
				String effectName = json["effect"];
				int effectId = effectLoader->getEffectIdByName(effectName.c_str());

				if (effectId == -1) {
					responseDoc["message"] = "Executed command";
					responseDoc["reason"] = "Effect not found";
					responseDoc["status"] = "failure";
					responseDoc["command"] = _command;
					responseDoc["component"] = _component;
					return responseDoc;
				}
				auto effect = effectLoader->effects[effectLoader->getEffectIdByName(effectName.c_str())];

				DynamicJsonDocument effectConfigChangeDoc(effects_configSetup_dynamicJsonDocument_size);

				deserializeJson(effectConfigChangeDoc, value.c_str());
				effect->changeEffectFieldValue(effectConfigChangeDoc);

				effectLoader->refreshCurrentEffect();

				DynamicJsonDocument updatedLed2EffectJson(effects_configSetup_dynamicJsonDocument_size);
				effectLoader->addToJson(&updatedLed2EffectJson, false, true);
				String response;
				serializeJson(updatedLed2EffectJson, response);
				ws.textAll(response);
			}
			break;
		case Sensor1:
		case Sensor2:
			if(command == setTempDangerEnabled) {
				auto sensor = component == Sensor1 ? sensor1 : sensor2;
				sensor->setTempDangerEnabled(value.toInt() != 0);
			}
			if(command == setTempDangerThreshold) {
				auto sensor = component == Sensor1 ? sensor1 : sensor2;
				sensor->setTempDangerThreshold(value.toInt());
			}
			break;
		case Fan1:
		case Fan2:
			if (command == setPercent) {
				auto fan = component == Fan1 ? fan1 : fan2;
				int newPercent = value.toInt();
				fan->setPercent(newPercent);
			}
			break;
		case Configuration:
			if (command == setDisplayBrightness) {
				config->setDisplayBrightness(value.toInt());
			}
			if(command == setDisplaySleep) {
				config->setDisplaySleep(value.toInt() != 0);
			}
			break;
		case Invalid:
		default:
			responseDoc["message"] = "Invalid component";
			responseDoc["status"] = "failure";
			responseDoc["component"] = _component;
			return responseDoc;
	}

	responseDoc["message"] = "Executed command";
	responseDoc["status"] = "success";
	responseDoc["command"] = _command;
	responseDoc["component"] = _component;

	return responseDoc;
}

void onWsEvent(AsyncWebSocket *webSocket, AsyncWebSocketClient *client, AwsEventType type, void *arg, uint8_t *data,
			   size_t len)
{

	if (type == WS_EVT_CONNECT) {
		client->printf("Hello Client %u :)", client->id());
		DynamicJsonDocument json(initial_ws_connect_dynamicJsonDocument_size);
		led1->addToJson(&json);
		effectLoader->addToJson(&json);
		fan1->addToJson(&json);
		fan2->addToJson(&json);
		sensor1->addToJson(&json);
		sensor2->addToJson(&json);
		config->addToJson(&json);
		String response;
		serializeJson(json, response);
		client->text(response);
	} else if (type == WS_EVT_DATA) {
		AwsFrameInfo *info = (AwsFrameInfo *) arg;

		if (info->final && info->index == 0 && info->len == len && info->opcode == WS_TEXT) {
			/*
			Serial.printf("ws[%s][%u] %s-message[%llu]: ", webSocket->url(), client->id(),
						  (info->opcode == WS_TEXT) ? "text" : "binary", info->len);
*/
			char *jsonString = (char *) data;
			DynamicJsonDocument json(1024);
			DeserializationError error = deserializeJson(json, jsonString);

			if (error || !json.containsKey("component") || !json.containsKey("command") ||
				!json.containsKey("value")) {
				DynamicJsonDocument errorDoc(128);
				errorDoc["reason"] = "No json, invalid json or other error";
				errorDoc["message"] = "Error in communication";
				errorDoc["status"] = "failure";
				String response;
				serializeJson(errorDoc, response);
				client->text(response);
			}

			DynamicJsonDocument responseDoc = handleWebSocketCommunication(json);
			String response;
			serializeJson(responseDoc, response);
			client->text(response);
		} else {
			DynamicJsonDocument doc(192);
			doc["reason"] = "Only single frame as a json string allowed for communication";
			doc["message"] = "Error in communication";
			doc["status"] = "failure";
			String response;
			serializeJson(doc, response);
			client->text(response);
		}
	}
}

void loop()
{
	esp8266React.loop();

	Serial.printf("Free heap: %d\n", ESP.getFreeHeap());
	delay(500);
}

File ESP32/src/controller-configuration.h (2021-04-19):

//Don't change this unless you are modifying the firmware
const String esp32Version = "2.0.0";

const int effects_configSetup_dynamicJsonDocument_size = 5120;
const int led2_dynamicJsonDocument_size = 256 + effects_configSetup_dynamicJsonDocument_size;
const int initial_ws_connect_dynamicJsonDocument_size = 1024 + led2_dynamicJsonDocument_size;


const int dhtSenseInterval = 2000;
const int led2NumberOfLeds = 60;
const int led2CurrentLimit = 1500;
const int led2Brightness = 80;

const int serial1BaudRate = 115200;
const int serial2BaudRate = 115200;

const int displayCompClickCheckInterval = 20;
const int displayBootDelay = 500;
const int displayGraphMinTemp = -10;
const int displayGraphHeight = 120;

//Every x half revolutions the rpm will be calculated so 120 means every 60 full rotations
//Needs to be dividable by 4 as it is also used for a small delay fanSenseInterval / 4 after each calculation.
const int fanSenseInterval = 120;

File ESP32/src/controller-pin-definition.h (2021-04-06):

const int dht22_1_pin = 19;
const int dht22_2_pin = 18;
const int fan1_tacho_pin = 13;
const int fan1_pwm_pin = 14;
const int fan2_tacho_pin = 27;
const int fan2_pwm_pin = 26;
const int buzzer_pin = 4;
const int led1_relay_pin = 21;
const int led2_data_pin = 22;

const int nextionDisplayRX = 16;
const int nextionDisplayTX = 17;

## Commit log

2020-07-22 updated display software. Fixed led2 mode problems some code improvements (switch). added more animations. added first parts for temperature warning.
    [main.cpp]
2020-07-22 Temperature warning. Added basic code logic for detecting temperature beeing above threshold. Updated Displays images to support temperature warning.
    [Configuration.h]
2020-07-23 Added Temperature Warning. Added buzzer logic for Temperature Danger. Cleaned up code a bit.
    [Configuration.h]
2020-07-23 Fixed fan2 pwm setting. fan2 was setting the dutyCycle of fan1.
    [main.cpp]
2020-07-23 Added Message/Warning Label to ESPUI.
    Will display Errors or Status reports like Temperature Warning/Danger.
    [main.cpp]
2020-07-28 fixed display sleep not working when using espui
    [main.cpp]
2020-07-28 Fixed espui button/switch again. Renamed switches from espui to espui_switch_... Added about tab content Added reboot button to espui Added configurable reboot to rather reboot than create hotspot.
    [Configuration.h]
2020-07-28 moved wifi configuration to Configuration.h
    [Configuration.h]
2020-07-28 Added WiFiManager Removed old Wifi logic. Removed fixed wifi ssid and password. Added description to configuration options. Added wifi reset button to espui
    [Configuration.h]
2020-07-28 Added WifiManager dark mode
    [Configuration.h]
2020-07-28 Fixed message page not changing on Wifi connect
    [main.cpp]
2020-07-29 Added temperature animation for led2. Renamed configuration for min temp
    [Configuration.h]
2020-07-29 Fixed led2 mode changing not reseting color
    [main.cpp]
2020-07-29 Removed wifi timeout, replaced with non blocking
    [Configuration.h]
2020-07-29 Added "needs led2 color to modes that need a color Moved rainbow mode to the bottom
2020-07-29 Fixed led2 mode not loading
    [main.cpp]
2020-07-29 Added back wifiManager timeout Added wifiManager blocking config Added missing configuration comments Added saving the led2_mode as String into flash
    [Configuration.h]
2020-08-26 Removed fans max rpm configuration.
    [Configuration.h]
2020-08-26 Fixed color changing not working. Changed to using crgb value for logic instead of converting to strings.
    [main.cpp]
2020-08-27 Moved some defines to new file ESP32 changes: Removed changing of button state on display Fixed led2 setting color not working like it should for black (off). Fixed led2 brightness not beeing 100% wh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
    [main.cpp]
2020-08-27 Fixed wrong brighness method on color setting.
    [main.cpp]
2020-08-27 Added "solid" mode as effect to prevent leds from beeing not bright enough.
    [main.cpp]
2020-08-27 Added GPLv3 Licence notice to the top of all files
    [Configuration.h]
2020-08-28 added PCB files. 1. The quality pcb files for ordering 2. The cnc pcb files for milling using a cnc mill (wider traces) this file is a bit older but is still working.
    [enclosure_controller_esp32.brd, enclosure_controller_esp32.sch]
2020-08-28 Renamed pcb to pcb version
    [enclosure_controller_esp32.brd, enclosure_controller_esp32.sch]
2020-08-28 Added fusion360 3d files both for pcb and cnc version
2020-08-28 Updated .gitignore to include BOM edit file Added BOM file for needed components (pcb version)
    [BOM.xlsx]
2020-08-28 Added Images of hardware and display pages
    [BOM.xlsx]
2020-08-28 Added image of pcb without components
2020-08-29 Fixed BOM file. Added missing 4 channel level shifter
    [BOM.xlsx]
2020-08-29 Fixed issue with degrees symbol on nextion display. Fixed sensor 2 setting values for sensor 1 on display. Changed check if dht value read is nan to atleast set the value that already works. Added Te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
    [Configuration.h]
2020-08-29 Changed Nextion tft file to include current version.
2020-08-29 Fixed wrong fanrpm value beeing set when on fans page. Removed Nextion library and replaced with own simplified SimpleNextion class.
    [main.cpp]
2020-08-30 Big changes incomming. Replaced original effects logic with dynamic loading of effects. Effects can now be self added and will be made available both tho the display and the ESPUI. Replaced storing/c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
    [main.cpp]
2020-08-30 Fix for new led effects logic. Added check if mode selected is larger than maximum (-1) Added check if current mode is not equal to "new" mode and only update animation then.
    [main.cpp]
2020-08-30 Removed unneded include Arduino.h from effect class files. Added example pictures for creating effects
2020-08-30 Fixed saved led2 mode not beeing shown on display/espui on boot.
    [main.cpp]
2021-04-02 Started reworking the firmware.
    - Moved some features to there own class.
    - Removed all the code and started from the beginning to reduce early created errors.
    - Implemented first basic features (sensor, fan, led1 relay, led2)
    [Configuration.h]
2021-04-03 Improved Sensor class.
    - Now .handle() call required.
    - Now uses esp32's tasks to read the sensor every <sense interval>.
    Fixed sense interval in config set to long instead of int.
    [Configuration.h]
2021-04-03 Improved Fan class with tasks.
    - Fan class now also uses tasks to set the rpm attribute.
    - not getFanSpeed function call required.
    - Added code to prevent empty loop function to cause watchdog crash
    [main.cpp]
2021-04-03 Added small delay after creating fan. Worked on implementing Nextion Display.
    - Added small delay after fan object creation just to make sure it won't cause trouble.
    - Implemented first functions for NextionDisplay.
    [Configuration.h]
2021-04-03 Reformatted code and fixed some spelling errors.
    [main.cpp]
2021-04-04 Added begin functions to classes to fix errors. Added nextion handling.
    - Fixed sensors always reading NaN (0.00 °C).
    - Added command handling for nextion display
    - Reworked how messages are send from the nextion display (made all components vscope global)
    - Removed all the code from the nextion display.
    - Nextion is now fully handled by ESP32 to prevent issues with communication.
    [Configuration.h]
2021-04-04 Nextion display implementation continued.
    [Configuration.h]
2021-04-04 Added logic for handling sliders for fan speed. Changed parameter compName to compVarName.
2021-04-04 Added esp8266-react as a webinterface.
    - Added esp8266-react and created/designed first pages.
    - Removed no longer used libs from platformio.ini (ESPUI, WifiManager, ...)
    - Moved general environment configuration in platformio.ini to the [env] environment
    [main.cpp]
2021-04-05 Implemented loading of data from the esp for sensors & fans.
2021-04-05 Added sensor temperature graphs to sensor tab.
2021-04-05 Designed the sensors page and added react redux + redux-toolkit to save data between pages.
2021-04-05 Started designing fan's page/tab. Added framer motion lib.
2021-04-06 Improved ValueField component and added value fields to sensors page.
2021-04-06 Added code for changing the fan speed from the webinterface.
2021-04-06 Moved functions from main.cpp to helper.h file. Potentially fixed esp32 crashing / rebooting a couble of times until it boots fully.
    [main.cpp]
2021-04-06 Added ability to configure what features to enable.
    [Configuration.h]
2021-04-06 Fixed setSpeed rest request not working
    [main.cpp]
2021-04-06 Worked on leds webinterface tab.
2021-04-07 Implemented EffectLoader for led2 effects.
2021-04-07 Improved led1 & led2 responses and webinterface usage.
2021-04-08 Started on reworking the connection using websockets instead of loop rest requests.
    [main.cpp]
2021-04-08 Added ability to check if sensor temperature or humidity changed. Improved nextion temp & humidity update.
2021-04-08 Changed sensors to use callback tasks when value changed.
2021-04-08 Finally found reason why esp32 kept loosing heap. Changed fan task to include a vTaskDelay to give the idle task some cpu time.
2021-04-09 Switched to using const char* for component names passed to constructors. Improved fan task a bit. Bringing more performance and less heap usage.
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2021-04-10 Changed Fan class to use events for dealing with rpm calculation & rpm update callback.
    - Removed creating a task every time the rpm callback needs to be called and switched to event groups.
    - Improved heap usage by using event groups.
    - Added documentation/comments to fan class.
2021-04-10 Added event usage to sensor class.
    - Sensor class now also uses events that get set when the temperature should update.
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2021-04-11 Added pwm update callback and event to fan. Fixed task event bits being wrong.
    - Added pwm callback that waits for the event to get triggered by the fans setDutyCycle or setPercent function.
    - Fixed setDutyCycle function not updating percent value
    - Fixed task event bits being wrong (they had to be unique) :D
    [main.cpp, task-events.h]
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2021-04-12 Websocket implementation for fans. - Added react env variable for redux-websocket prefix. - Added sync of percent, rpm and duty cycle to fans page. - Added back web socket message handling.
2021-04-12 Fixed some issues with led1 and led2.
    [main.cpp, task-events.h]
2021-04-17 Fixed wrong icon color. Increased size of arrows for the led2 mode switching.
2021-04-17 Fixed fan issues. Implemented led 2 effect changing using the nextion display.
    - Possibly fixed issue that would cause fan1 to cause the esp to crash when reading the percent value.
    - Implemented led2 effect changing and sync on the nextion display.
    - Changed where values in fan class are initialized.
    [main.cpp]
2021-04-17 Created newMap function that replaces the arduino map and makes sure the values don't exceed outMin and outMax.
    [main.cpp]
2021-04-17 Main page with websocket and improvements
    - Changed main page to use websocket instead of no longer used/working rest api call.
    - Added redux select to get both sensors as an array (selectSensors).
    - Improved ValueField component to use up 100% width when nothing else is there.
    - Updated nextion file with latest changes.
2021-04-17 Effect config setup
    - Implemented a way to setup config values. These can then be used in the webinterface to create a config for a led2 effect (ex.: effect "solid" => array of supported colors).
    - Added missing key to main page map PaperSection.
    - Added configSetup for solid effect.
    - Added config variables for defining some of the jsonDoc sizes.
    [controller-configuration.h]
2021-04-18 Effect update handling and fixing
    - Fixed wrong message when invalid component or invalid command send (would send int instead of name of component as string).
    - Added wsSend for effect config changing.
    [main.cpp]
2021-04-18 Effect update handling
    - Added code for handling effect config value changes.
    - Added code for updating led2 effect config values.
    - Set upload_speed to 921600 in platformio.ini.
    - Fixed switches in led2 effect config form missing default value.
    - Removed config fields in the solid effect used for testing.
    [main.cpp]
2021-04-18 Added updating of the Led2EffectConfigForm when the state changes.
    - Will update the form for all currently connected websockets (so that users don't have to refresh the page to see the changes live).
2021-04-18 Added code that allos reading of a select & switch value from the config json doc. Added code for changing the color of the solid effects color.
2021-04-19 Changed switch field to also use "value" for storing the current value instead of "state".
2021-04-19 Fixed switching from a different effect to the "none" effect causing react exception.
2021-04-19 Running effect added.
    - Added numberOfLeds field to effect class in case it is needed at some point
2021-04-20 Created card component and replaced PaperSection on sensor page with cards
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2021-04-21 Added animation to led 2 effect configuration. Added missing default state for selects array.
2021-04-24 Added configuration page and class in esp32 code to store display brightness.
2021-04-24 Added save to flash button to configuration tab.
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2021-04-24 Add state updating for fan spin animation switch
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2021-04-24 Change file extension of EnclosureController component to js (javascript)
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2021-04-24 Added rendering sensor graphs if enabled in webinterface config.
2021-04-24 Added hiding of the action card/action buttons when graph is disabled
2021-04-26 Added display sleep configuration option. Reworked config object updating to always update the whole config to reduce number of events & callbacks for each config option.
    [main.cpp, task-events.h]
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2021-04-26 Renamed temp warn in sensor state to "tempWarn" instead of "warning"
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2021-04-26 Replaced mapping for sensor fields to manual creation of all fields.
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2021-04-26 Fixed sensor temp and humidity update deleting tempWarn field.
    [main.cpp]
2021-04-26 Changed SwitchCard component to return value in onChange instead of event.
2021-04-26 Changed leds page to use SelectCard component for led2 effect.
2021-04-26 Added fields for warning & danger threshold for sensor temperatures.
2021-04-26 Added borders around sensor card when warning got triggered. Fixed sensor2 updates sending wrong data.
    [main.cpp]
2021-04-26 Moved code for setting a sensor into separate function called by both sensors.
2021-04-26 Replaced temp warning & temp danger with single temp danger.
    [main.cpp]
2021-04-26 Added save button to InputCard component to prevent mass sending commands
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

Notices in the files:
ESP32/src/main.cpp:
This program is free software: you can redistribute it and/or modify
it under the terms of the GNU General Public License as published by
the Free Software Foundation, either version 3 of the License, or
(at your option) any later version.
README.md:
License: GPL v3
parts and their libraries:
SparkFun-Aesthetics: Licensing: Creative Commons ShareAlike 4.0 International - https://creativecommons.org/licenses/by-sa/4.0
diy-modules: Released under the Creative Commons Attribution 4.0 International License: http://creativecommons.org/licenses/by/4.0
